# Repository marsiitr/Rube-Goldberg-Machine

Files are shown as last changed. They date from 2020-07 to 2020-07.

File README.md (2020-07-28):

<p align="justify">
  <h1>Rube-Goldberg-Machine</h1>
  <h2>Srishti 2020</h2>
</p>

<p align="center">
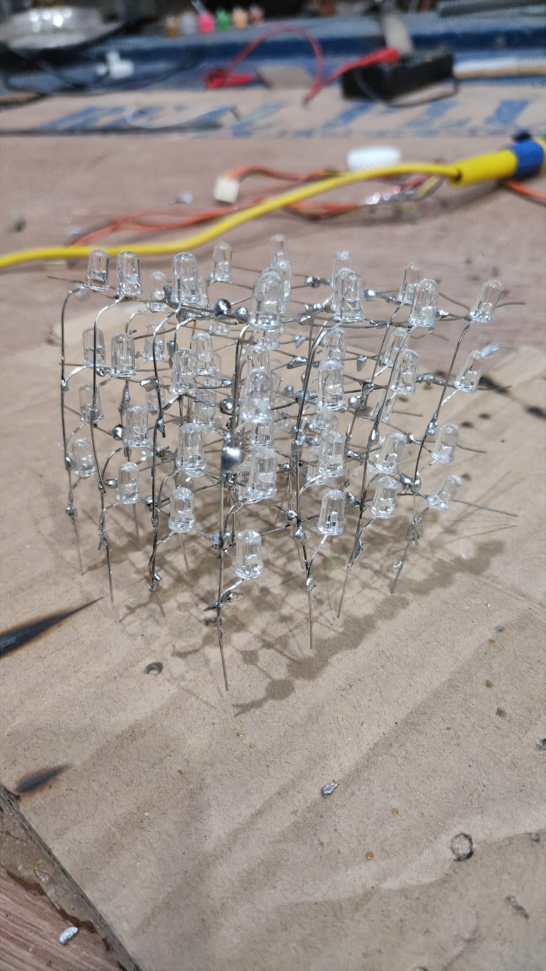
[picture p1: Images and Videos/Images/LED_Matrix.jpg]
LED Matrix
  
  <i>LED Matrix</i>
</p>

<p align="justify">
  <h2>Abstract</h2>
  <p>A Rube Goldberg Machine is a contraption intentionally designed to perform a simple task in an indirect and overly complicated way. The aim of this project is to depict the life of a college student through a similar complex assembly of mechanical and electronic components linked with each other creating a metaphor between humans and machines.</p>
</p>

<p align="justify">
  <h2>Motivation</h2>
  <p>College life may seem to be full of excitement and surprises for a layman, but little do he know of the struggles that the student had to face to reach that milestone and the difficulties that are masked by the brand college name. So our team of 5 freshers decided to cover the important moments of the journey beginning with exams to the major events of 1st year and what we think is to come next for us. We attempt to display it in a visually appealing format making use of our mechanical and electronics expertise.</p>
</p>

<p align="justify">
  <h2>Workflow</h2>
</p>

<p align="center">
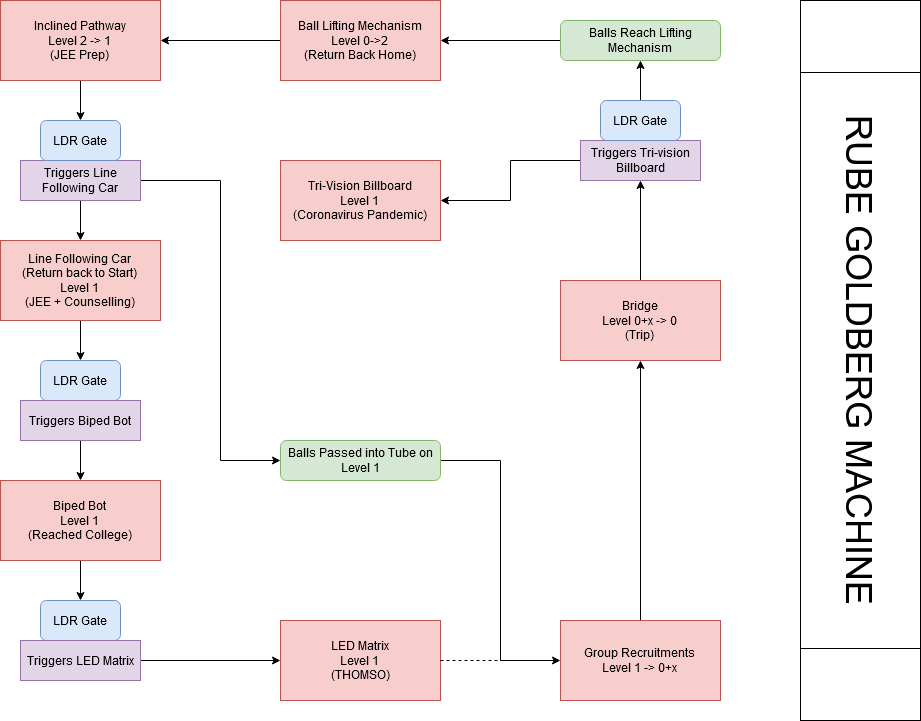
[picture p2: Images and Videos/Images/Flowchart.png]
Flowchart
  
  <i>Schematic Flow Chart of the Machine</i>
</p>

<p align="justify"> 
  
* The entire project is divided into 8 major elements depicting a distinct phase in the life of a student who is represented by spherical balls of different sizes. 

* The Tower of Exams(Inclined Pathway) illustrates the ups and downs, successes, and failures in each of the competitive exams. 

* The First LDR Gate represents the path to the major JEE Exam after which students seek admission to colleges through counselling and finally enter college after years of hard work.

* Similar to the biped bot, the students stumble here and there in the college exploring various things and then comes the first major college cultural fest of their lives, THOMSO, depicted using LED Cube. 

* Entering the next semester, students are overwhelmed with all the campus groups releasing recruitment notices.

* After this stressful and dilemmatic process comes the adventurous trip which is depicted by the bridge (Lakshman Jhula,  Rishikesh). 

* Next comes the second semester’s Mid-Term Examinations and following End-Term Examinations which is well shown by the Trivision Billboard. 

* Summer breaks are depicted by the Ball lifting mechanism and the journey goes on for the next and their next batch of freshers as our Rube Goldberg machine works in a loop.

</p>

<p align="justify">
  <h2>Mechanical Aspect of the Design</h2>
  <p>Rubber balls 3 of radius 2.5 cm and 3 of radius 3 cm each are used to denote the students.<br>The following steps help one understand the journey by providing a mechanical description of every component:
  <br>
  
* **Tower of Exams:** A vertical assembly of MDF towers inter-connected via loophole paths describes the difficult journey before getting into IIT.

  <p align="center">
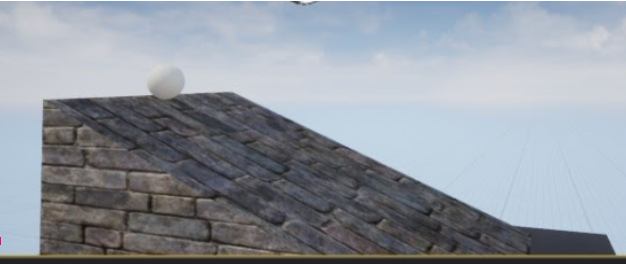
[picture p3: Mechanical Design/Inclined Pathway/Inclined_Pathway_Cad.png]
Tower of Exams
   <br>
    <i>Tower of Exams</i>
  </p>
  
* A smooth MDF path transitions into the LDR Gate triggering the **Line-following car**. Running on a parallel track is another MDF platform taking each ball to the chain lift.
  </p>

  <p align="center">
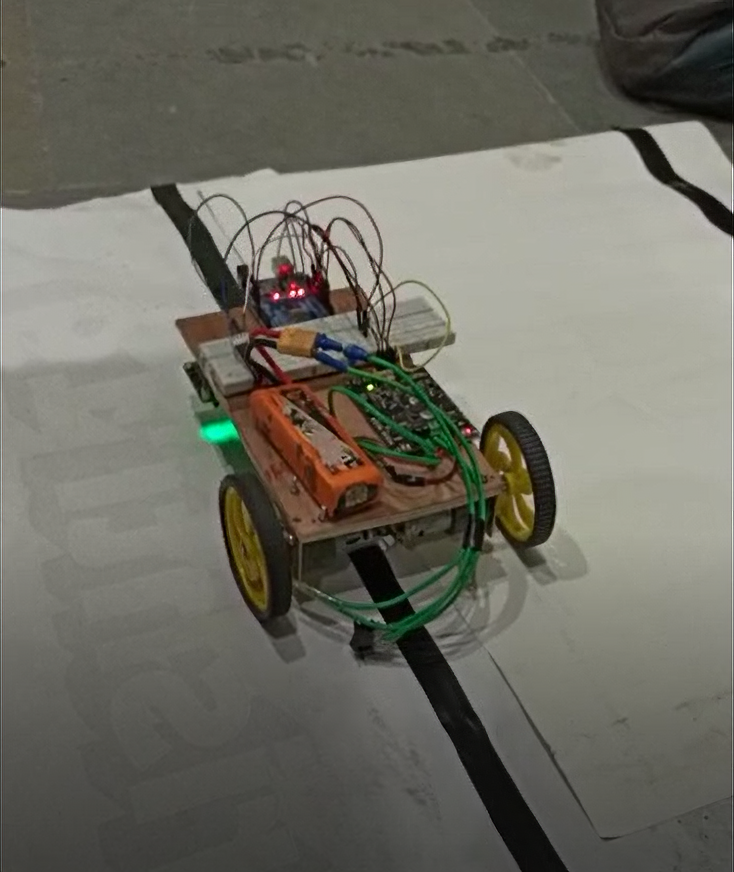
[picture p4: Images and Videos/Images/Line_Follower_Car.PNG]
Line Following Car
    <br>
    <i>Line Following Car</i>
  </p>

  <p>
 * Line-follower traverses through the loop and then triggers the Biped Bot.
  
 * **Biped bot** is a working prototype of a two-legged robot built with an assembly of 3 acrylic pulleys linked with elastic bands and 6mm steel rods, propelled by using a simple DC motor. It mounts an Arduino Uno on one side used to control the motor via a motor driver.
 
  </p>

<p align="center">
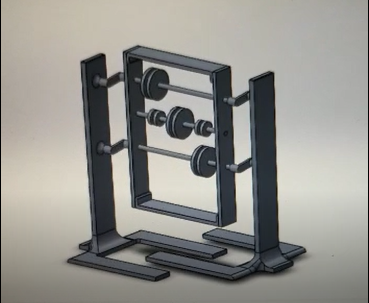
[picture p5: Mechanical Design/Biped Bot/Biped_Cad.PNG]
Biped Bot
  <br>
  <i>Biped Bot</i>
</p>

<p>
  
* Biped Bot passes through the LDR gate triggers the LED Matrix.

* Meanwhile, the balls approach the **Group Recruitment Phase** where they pass through a series of loopholes and get segregated as per their size.

<p align="center">
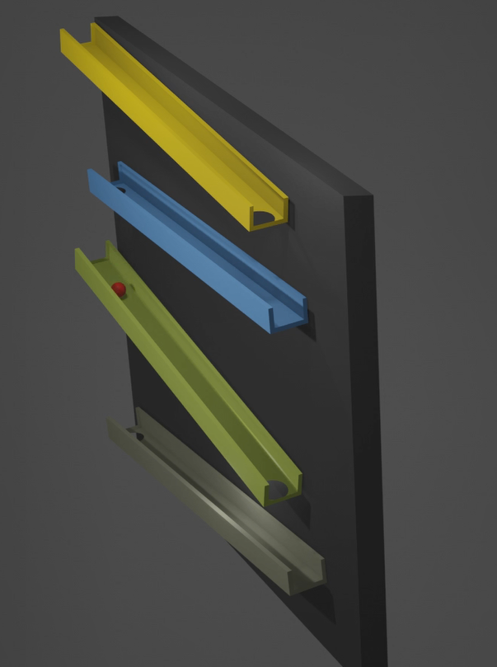
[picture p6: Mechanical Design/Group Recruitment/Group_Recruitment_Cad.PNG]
Group Recruitment Phase
  <br>
  <i>Group Recruitment Phase</i>
</p>

* The balls then trigger the final LDR gate activating the **Tri-Vision Billboard**.It is an assembly of 3 triangular prism-shaped boxes made using MDF and L-brackets mounted on a gear each through steel shafts held in place using a Plywood base and are free to rotate about its axis. A stepper motor is coupled with a driving gear, which transmits the actuation to all the three parts of the billboard, also employing two idler gears, so that all the prisms rotate in the same direction and in phase with each other. The gears and the base have been carefully 3d printed in the Tinkering Lab. [Reference](https://www.youtube.com/watch?v=uCx9riKxTvY&feature=youtu.be) (Heavily modified from the mentioned reference).

</p>

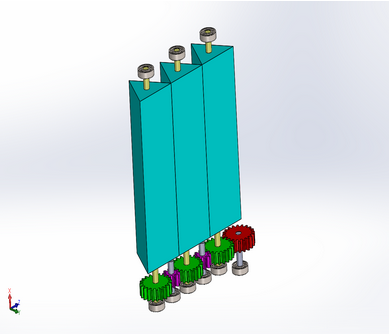
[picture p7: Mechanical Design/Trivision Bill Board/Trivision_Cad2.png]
Trivision Bill Board
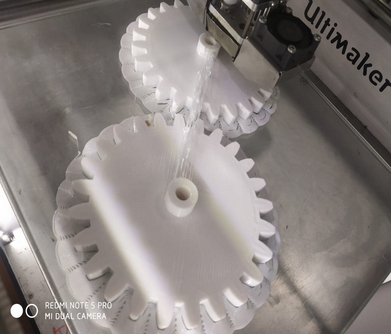
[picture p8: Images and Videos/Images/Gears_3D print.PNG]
Gear 3D print
 

<p>
  
* In the end, a **chain lift mechanism** lifts the balls back to level 1. The mechanism uses a 48-inch ladder chain and sprockets powered by a 12V DC motor. [Reference](https://www.youtube.com/watch?v=E2Yy66IbVuw&feature=youtu.be)
</p>
</p>

<p align="justify">
  <h2>Electronics Aspect of the Design</h2>
  <h3>Microcontroller</h3>
  <p>Arduino Uno 2560 R3 is used as the microcontroller board in each of the bots.</p>
  <h3>Hardware Architecture of the Line Following Car</h3>
</p>

<p align="center">
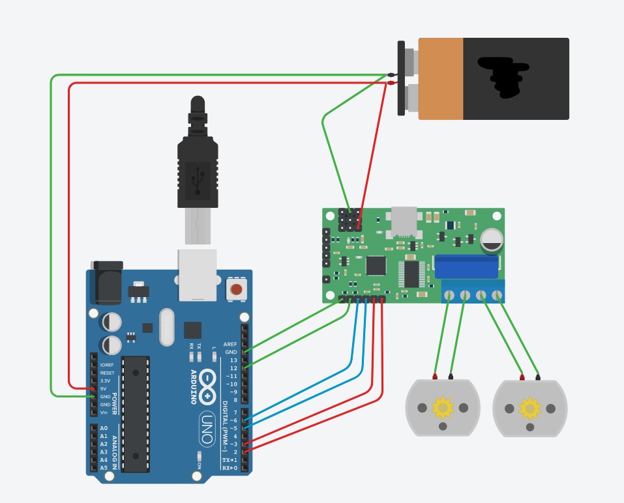
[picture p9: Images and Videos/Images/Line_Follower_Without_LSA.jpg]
Connections without the LSA
  <br>
  <i>Connections without the LSA</i>
</p>

### LSA Connections to Arduino
| LSA08 pin | Arduino Uno board |
|:-----:|:---:|
| 1 | RX (pin 0) |
| 2 | TX (pin 1)|
| 3 | Digital (pin 2) |
| 4 | Not Used |
| 5 | Digital (pin 4)|
| 6 | Not Used |
| 7 | Not Used|
| 8 | Not Used |
| 9 | Vin |
| 10 | GND |

<p align="justify">
  <h3>LSA08 Settings:</h3>
  <p>LINEMODE: Dark-ON detecting black line in white background.
  
  THRESHOLD: 7
  
  JUNCTION WIDTH: 8
  
  LSA gives 1 byte output data ranging from 0-70 with 35 being the base level.
  
  <h3>Working Principle</h3>
</p>

<p align="center">
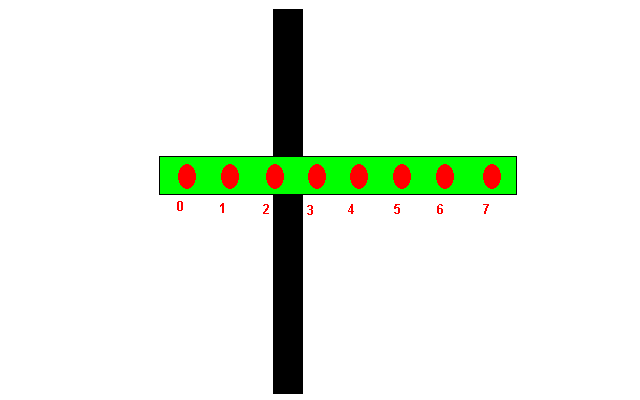
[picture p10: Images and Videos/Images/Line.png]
LSA Sensor Logic
  <br>
  <i>LSA Sensor Logic</i>
</p>

<p align="justify">
  <p>The car remains stable and follows the straight line if Level=35.
  For Level<35 : Speed of the left motor increases such that it comes back on track by moving to the right.
  For Level>35 : Speed of the right motor increases such that it comes back on track by moving to the left.</p>
    <h3>PID</h3>
    <p>PID is short for proportional, integral, and derivative. The PID is used to correct the error of the bot while traversing.
The correction value is given as
Correction = kp(error) + kd(error- previous_error)
<h3>Biped Bot</h3>
<p>A DC motor interconnected to three pulleys using bands which is responsible for the movement of a bipedal bot was driven by a motor driver which is connected to the Arduino Uno, battery, and also to HC-05 (which is used to pair Bluetooth) through a common ground. HC - 05 is also connected to the Arduino Uno through which the instructions given from the phone via Bluetooth can be transmitted to the Arduino Uno and so to the Motor Driver. The speed of the motor and direction can be controlled using the Bluetooth module.</p>

<p align="center">
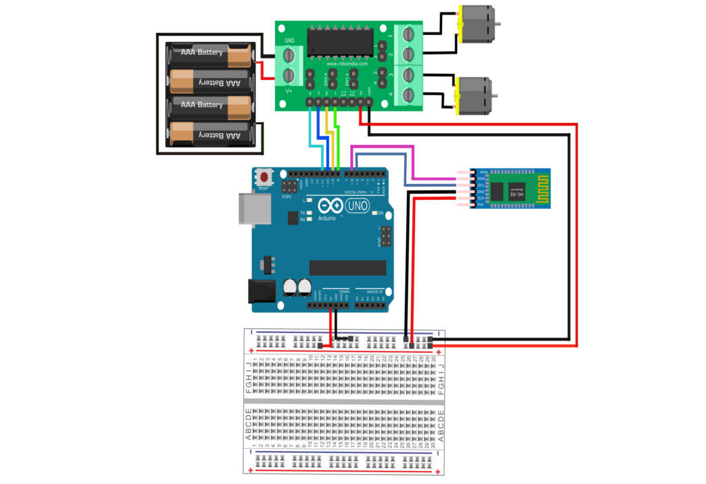
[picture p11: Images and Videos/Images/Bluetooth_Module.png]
Biped Bluetooth Module Connections
  <br>
  <i>Biped Bluetooth Module Connections</i>
</p>

<h3>LED Matrix</h3>
<p>It is a cube matrix built using 64 Light Emitting Diodes(LEDs, blue coloured) carefully soldered, and is capable of displaying various patterns as per the code fed into it.</p>

<h3>Trivision Billboard</h3>
<p>Uses a stepper motor to control the movement of the steel shafts about its axis controlled through the L298A motor driver.</p>

<h3>Chain Lift</h3>
<p>Uses a 12V DC Gear motor to rotate the chain vertically stabilized via sprockets.</p>

<p align="center">
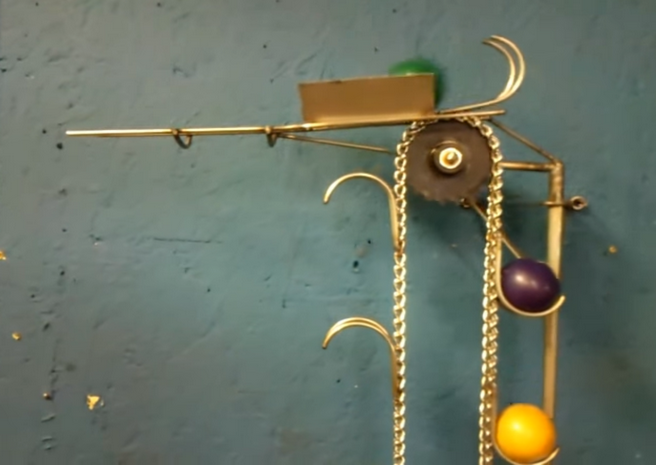
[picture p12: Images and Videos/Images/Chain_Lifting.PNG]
Chain Lift
  <br>
  <i>Chain Lift</i>
</p>

<h3>LDR Gate</h3>
<p>A simple setup of an LDR along with an Arduino Uno board is used to trigger elements in various places throughout the loop.</p>
<p align="center">
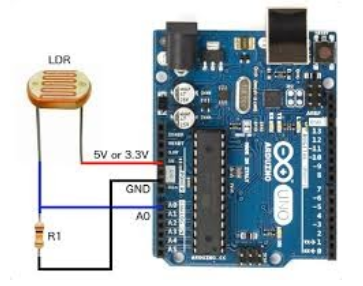
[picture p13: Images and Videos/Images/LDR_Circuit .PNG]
LDR
  <br>
  <i>LDR Connections</i>
</p>

<h3>Motor Driver</h3>
<p>We have used the Cytron MDD10A and L298A motor drivers. MDD10A is a dual-channel version of the MDD10C. Like MDD10C, MDD10A also supports locked-antiphase and sign-magnitude PWM signal.</p>
</p>

<p align="justify">
  <h2>Cost Structure</h2>
</p>

| Components | Quantity | Cost (in INR) |
|:---:|:---:|:---:|
| Auto-Calibrating Line Sensor LSA08 | 1 | 5000 |
| Arduino Uno Rev3 | 5 | 2000 |
| Digital LDR Module | 4 | 400 |
| LED | 64 | 100 |
| Cytron Dual Channel Enhanced 13Amp DC Motor Driver | 4 | 8000 |
| LiPo Battery 11.1V | 5 | 1500 |
| Motor Bracket | 2 | 200 |
| DC Motor | 1 | 300 |
| Stepper Motor | 1 | 500 |
| HC-05 | 1 | 300 |
| 48 inch Stainless Steel Ladder Chain | 1 | 1000 |
|Other components| | 1000  |
|Total Cost| | 20300  |

<p align="justify">
  
  <h2>Applications</h2>
  <p>The project succeeds in providing a visual description of a student's life.</p>
  
  <h2>Limitations</h2>
  
  <p>
  
* Some of the systems are not mechanically and electronically robust. For eg: The platforms used to carry the balls are hand-crafted and hence prone to obstruct the paths.

* Although an attempt was made to automate all the things and create a loop, several phases in the project still require manual handling. For eg: We need to collect the balls sorted and collected in the group recruitment phase and place them back in the starting point.

* Due to the Covid-19 pandemic, the actual Srishti event got cancelled. This created the most terrible impact as our team could not manufacture some of the parts like the chain lift mechanism. 
</p>
<h2>Future Improvement</h2>
<p>
  
* Manufacture the remaining components and make the project display-ready.

* Include several components for automating the process. A Ball-collecting bot making use of OpenCV for ball detection can be made to address this issue. It will significantly help to reduce the amount of manual work required to make the platforms.

</p>
<h2>Team Members</h2>

<p>
  
1. [Pradnesh Chavan](https://github.com/prady39)
2. [Rohit Kulkarni](https://github.com/roku01)               
3. [Shruti Gour](https://github.com/ShrutiGour)
4. [Shubham Kumar](https://github.com/shubhamr2701)
5. [Stuti Lilani](https://github.com/stuts23)
  
</p>
<h2>Mentors</h2>
<p>
  
1. [Kshitij Bithel](https://github.com/KSHITIJBITHEL)
2. Tabish Madni
3. [Yashutosh Bansal](https://github.com/yashutoshbansal)

</p>
<h2>References</h2>

<p>
  
- [Chain Lift](https://www.youtube.com/watch?v=E2Yy66IbVuw&feature=youtu.be)
- [Tri Vision Bill Board](https://www.youtube.com/watch?v=uCx9riKxTvY&feature=youtu.be)
- [Bluetooth Module](https://roboindia.com/tutorials/motor-control-with-bluetooth-module-hc-05/)
- [Line Follower Simulation](https://www.youtube.com/watch?v=vfwxKjOr-7o)
- [Line Following Car](https://tutorial.cytron.io/2015/07/31/line-following-robot-using-lsa08-serial-mode-digital-output/)

</p>

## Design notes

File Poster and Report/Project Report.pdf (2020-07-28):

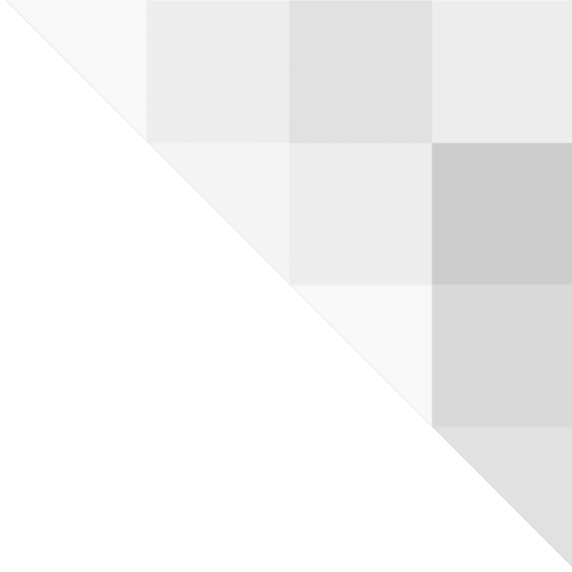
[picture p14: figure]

# Rube Goldberg Machine

# Srishti 2020

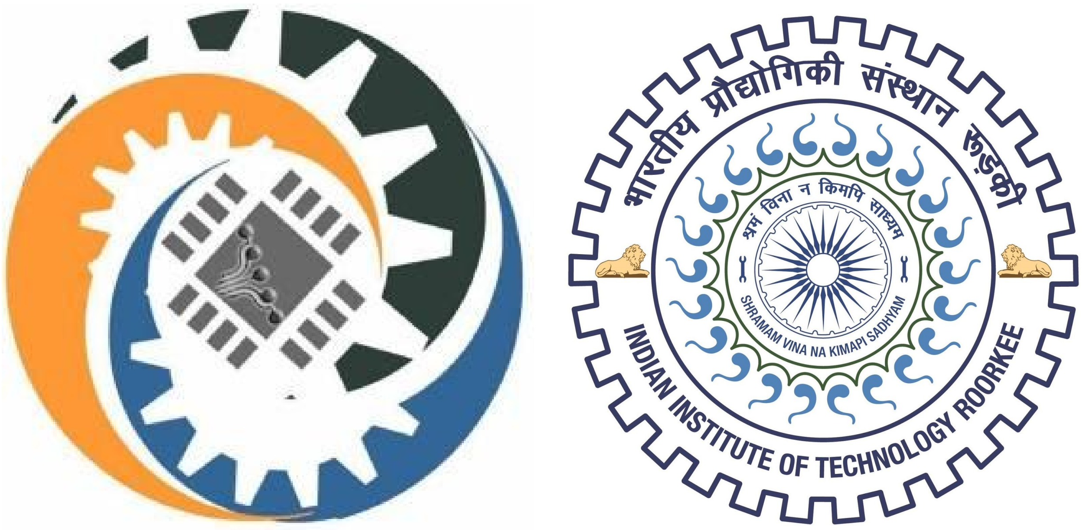
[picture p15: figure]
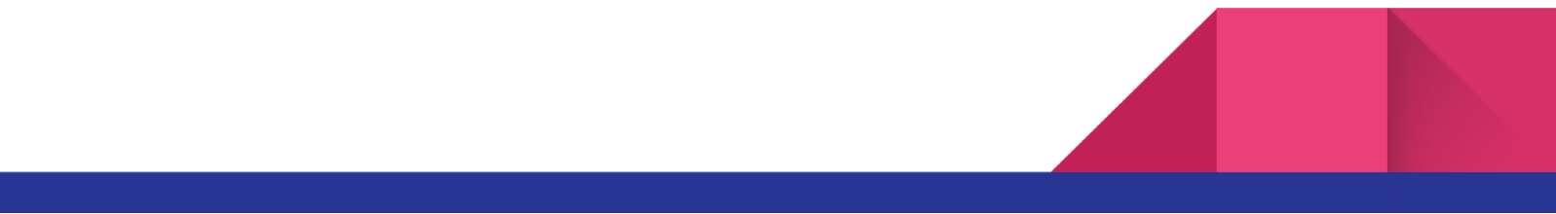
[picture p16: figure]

# Team Members

## Pradnesh Chavan Rohit Kulkarni Shruti Gour Shubham Raut Stuti Lilani

# Mentors

## Kshitij Bithel Tabish Madni Yashutosh Bansal

# Contents

## ➔Abstract ➔Project Motivation ➔Elements and Linkages ➔Mechanical Aspects of the Project ➔Electronics Aspects of the Project ➔Cost Structure ➔Applications ➔Limitations ➔Future Improvement ➔Acknowledgments

# Abstract

A Rube Goldberg Machine is a contraption intentionally designed to perform a simple task in an indirect and overly complicated way. The aim of this project is to depict the life of a college student through a similar complex assembly of mechanical and electronic components linked with each other creating a metaphor between humans and machines.

# Project Motivation

College life may seem to be full of excitement and surprises for many, but little do they know of the struggles that the student had to face to reach that milestone and the difficulties that are masked by the brand college name. So our team of 5 freshers decided to cover the important moments of the journey beginning with exams to the major events of 1st year and what we think is to come next for us. We attempt to display it in a visually appealing format making use of our mechanical and electronics expertise.

# Elements and Linkages

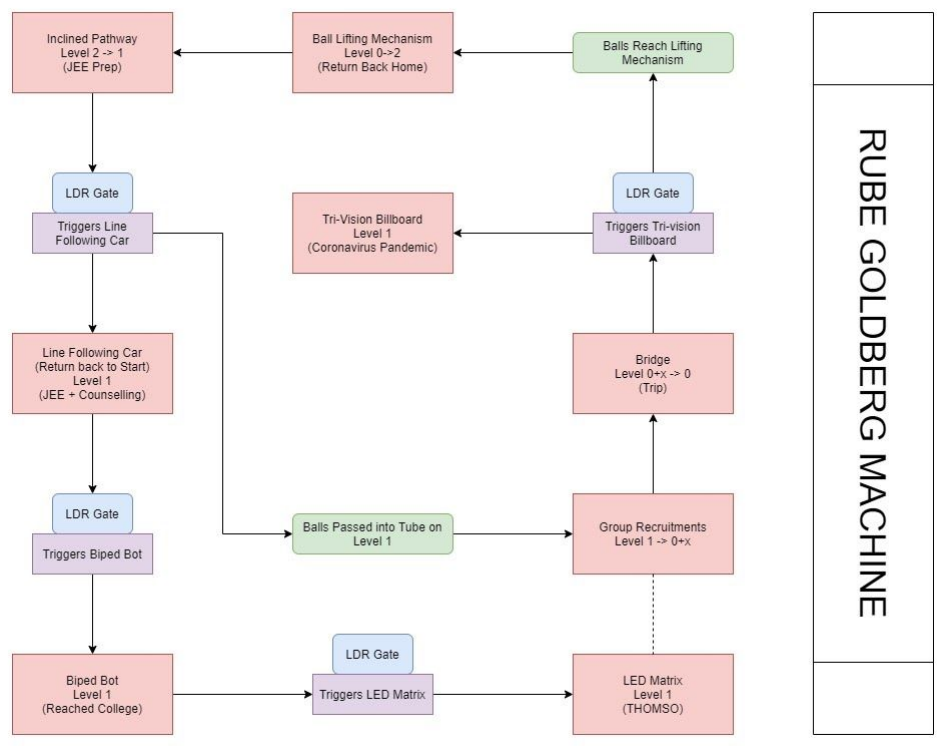
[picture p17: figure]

- The entire project is divided into 8 major elements depicting a distinct phase in the life of a student who is represented by spherical balls of different sizes.
- The Tower of Exams(Inclined Pathway) illustrates the ups and downs, successes, and failures in each of the competitive exams.
- The First LDR Gate represents the path to the major JEE Exam after which students seek admission to colleges through counseling and finally enter college after years of hard work.
- Similar to the biped bot, the students stumble here and there in the college exploring various things many of which are new to them and then comes the first major college fest of their lives, THOMSO, depicted using LED Cube. The matrix laden with its bright colors succeeds in depicting the aura of the fest.
- Entering the next semester, students are overwhelmed with all the groups releasing recruitment notices. This period involves a lot of stress and confusion, but it is fun nevertheless.
- After this stressful and dilemmatic process comes the adventurous trip which is depicted by the bridge (Lakshman Jhula, Rishikesh).
- Next comes the second semester’s Mid-Term Examinations and following End-Term Examinations which is well shown by the Trivision Billboard.
- Then we all head back to our respective hometowns for spending the summer breaks that are depicted by the Ball lifting mechanism and the journey goes on for the next and their next batch of freshers as our Rube Goldberg machine works in a loop.

# Mechanical Aspect of the Design

Rubber balls 3 of radius 2.5cm and 3 of radius 3cm each are used to denote the students.
The following steps help one understand the journey by providing a mechanical description of every component:
1. Tower of Exams: A vertical assembly of MDF towers inter-connected via loophole paths describes the difficult journey before getting into IIT.

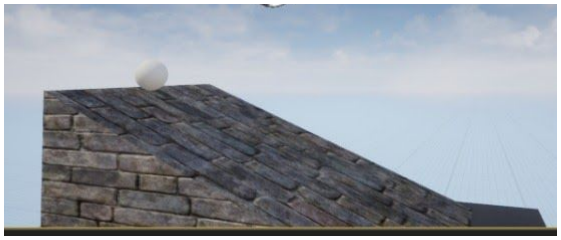
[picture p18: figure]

2. A smooth MDF path transitions into the LDR Gate triggering the Line-Following Car. Running on a parallel track is another MDF platform taking each ball to the chain lift. Line-follower traverses through the LDR gate and then triggers the Biped Bot.

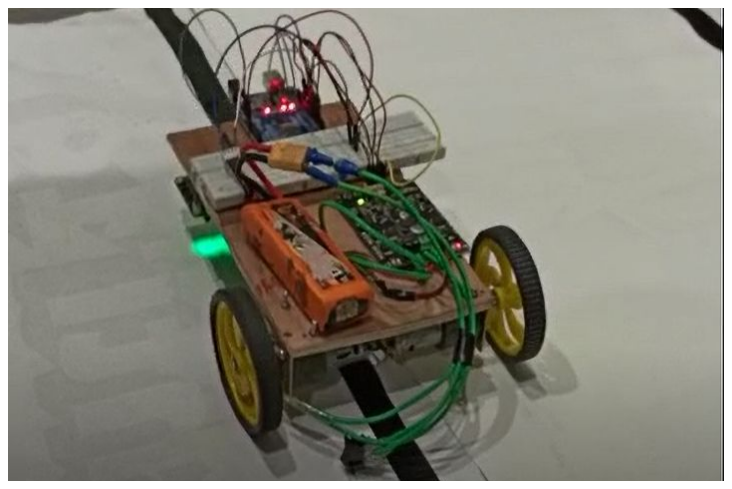
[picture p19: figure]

3. Biped bot is a working prototype of a two-legged robot contained in an MDF frame with an assembly of 3 big and 2 small acrylic pulleys linked with elastic bands and held in place by 6mm shafts, propelled by using a simple DC motor. It mounts an Arduino Uno on one side to control the motor via a motor driver. Reference (https://youtu.be/Z7N0xCDVzIA)

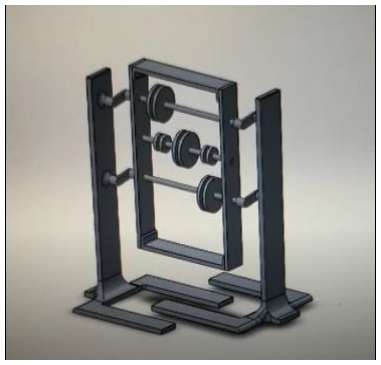
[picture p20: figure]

4. The Biped Bot passes through the LDR gate and triggers the | LED Matrix | .

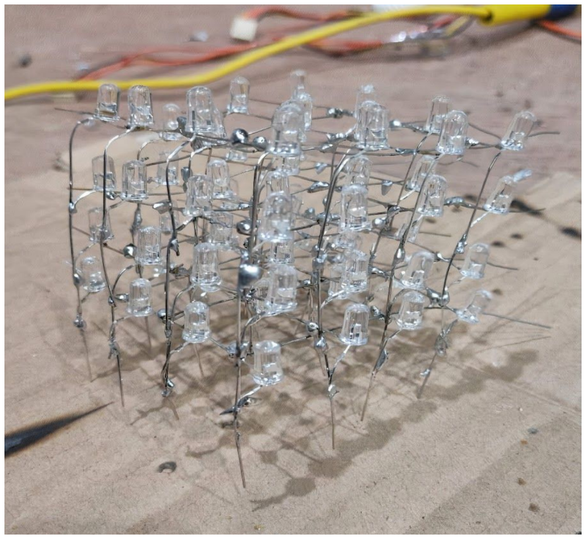
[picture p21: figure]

5. Meanwhile, the balls approach the Group Recruitment Phase where they pass through a series of inclined ramps that contain holes at their ends and get segregated along the way as per their size. This symbolizes the segregation of students into various tech and cultural groups based on their skills and interests.

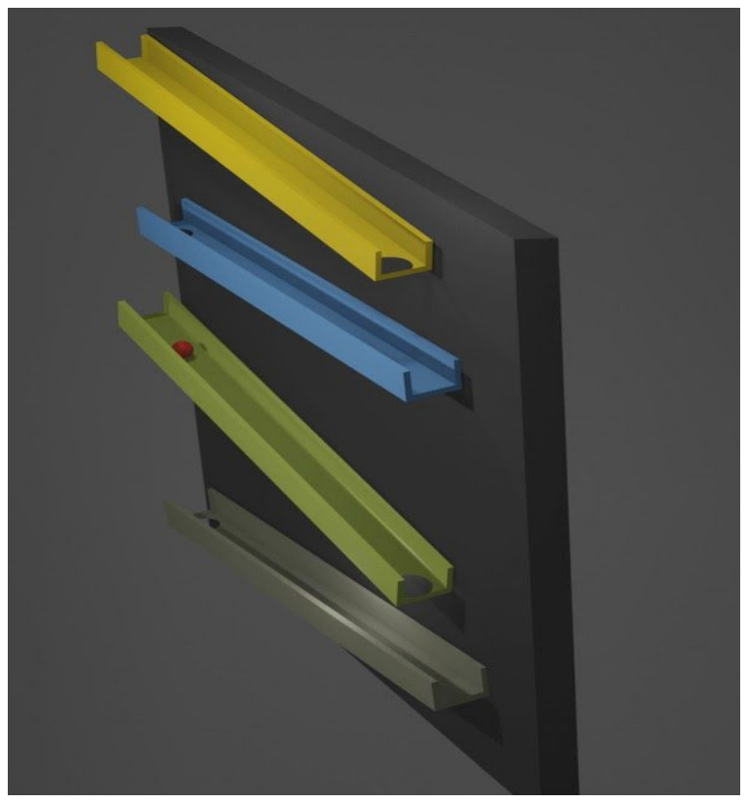
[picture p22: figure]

6. The balls emerge from the Group Recruitments at a certain height above the ground level and roll down a slope passing through a simple bridge made using cardboard. This signifies the trips that students go on after the onset of the spring season. After this, the balls pass through another LDR gate and trigger the next element.
7. Balls then trigger the final LDR gate activating the Tri-Vision Billboard . It is an assembly of 3 triangular prism-shaped boxes made using MDF and L-brackets mounted on a gear each through steel shafts held in place using a Plywood base and are free to rotate about its axis. A stepper motor is coupled with a driving gear, which transmits the actuation to all the three parts of the billboard, also employing two idler gears, so that all the prisms rotate in the same direction and in phase with each other. The gears and the base have been carefully 3d printed using PLA in the Tinkering Lab. Reference (https://youtu.be/uCx9riKxTvY) (Heavily modified from the aforementioned).

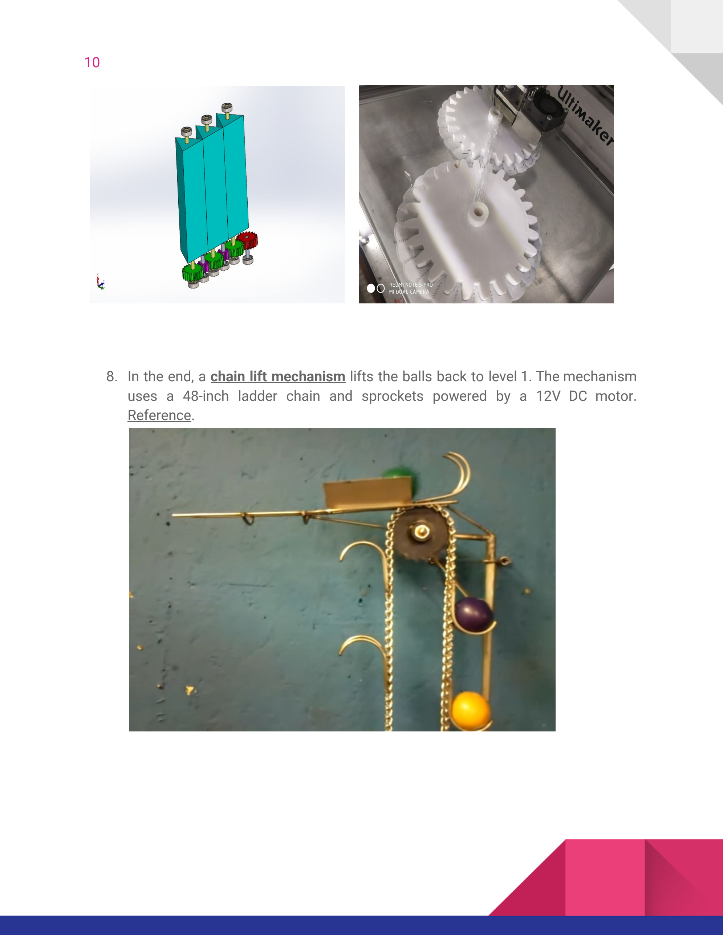
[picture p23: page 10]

8. In the end, a chain lift mechanism lifts the balls back to level 1. The mechanism uses a 48-inch ladder chain and sprockets powered by a 12V DC motor. Reference (https://www.youtube.com/watch?v=E2Yy66IbVuw&feature=youtu.be) .

# Electronics Aspect of the Design

Microcontroller: Arduino Uno 2560 R3 is used as the microcontroller board in each of the bots.

## Line Following Car:

Hardware Architecture of the Line Following Car:

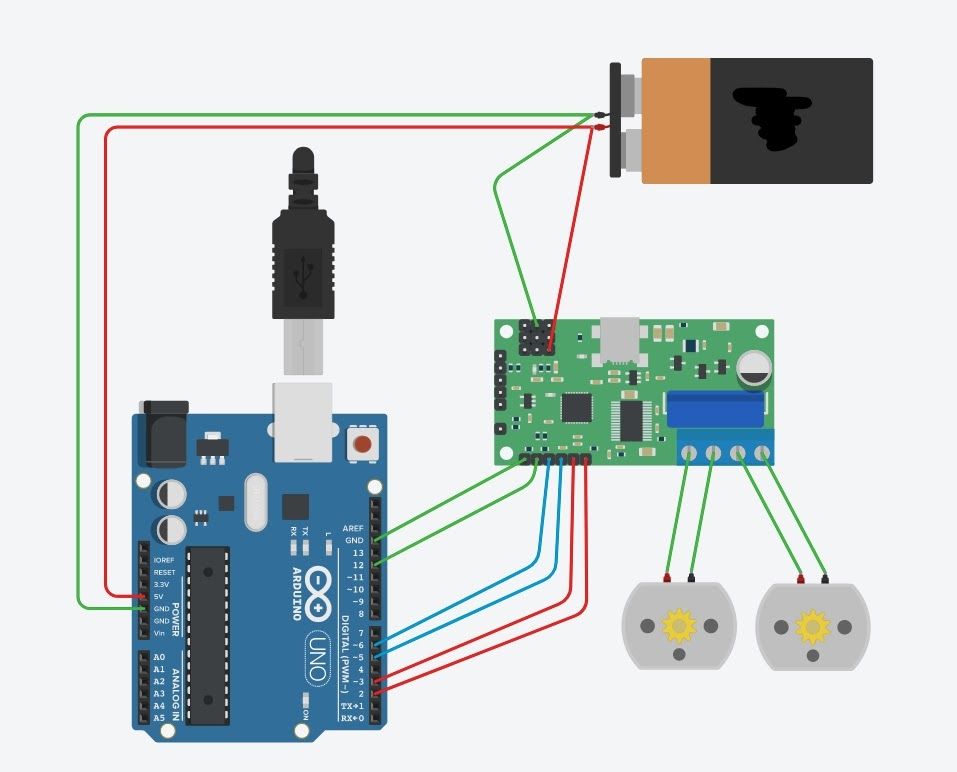
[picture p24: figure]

LSA CONNECTION TO ARDUINO

LSA08 Pin | Arduino Uno board
1 | RX (pin 0)
2 | TX (pin 1)
3 | Digital pin 2
4 | Not Used
5 | Digital pin 4
6 | Not Used
7 | Not Used
8 | Not Used
9 | Vin
10 | GND

LSA08 Settings:
LINEMODE: Dark-ON detecting black line in white background.
THRESHOLD: 7
JUNCTION WIDTH: 8

LSA gives 1-byte output data ranging from 0-70 with 35 being the base level.

Working Principle:

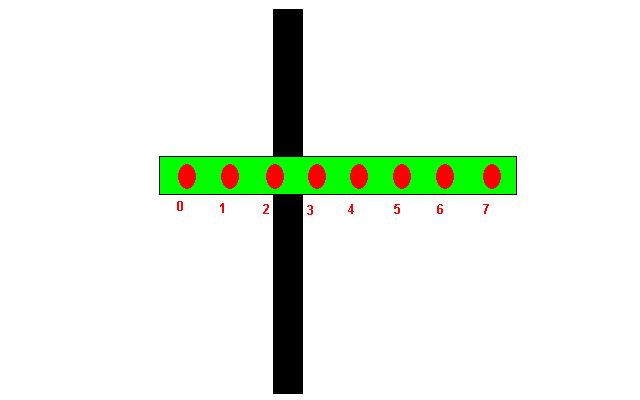
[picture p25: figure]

The car remains stable and follows the straight line if Level=35.
For Level<35: Speed of the left motor increases such that it comes back on track by moving to the right.
For Level>35: Speed of the right motor increases such that it comes back on track by moving to the left.

PID:

PID is short for proportional, integral, and derivative. The PID is used to correct the error of the bot while traversing.

The correction value is given as

Correction = kp(error) + kd(error- previous_error)

## Biped Bot:

A DC motor interconnected to three pulleys using bands which is responsible for the movement of a bipedal bot was driven by a motor driver which is connected to the Arduino Uno, battery, and also to HC-05 (which is used to pair Bluetooth) through a common ground. HC - 05 is also connected to the Arduino Uno through which the instructions given from the phone via Bluetooth can be transmitted to the Arduino Uno and so to the Motor Driver. The speed of the motor and direction can be controlled using the Bluetooth module.

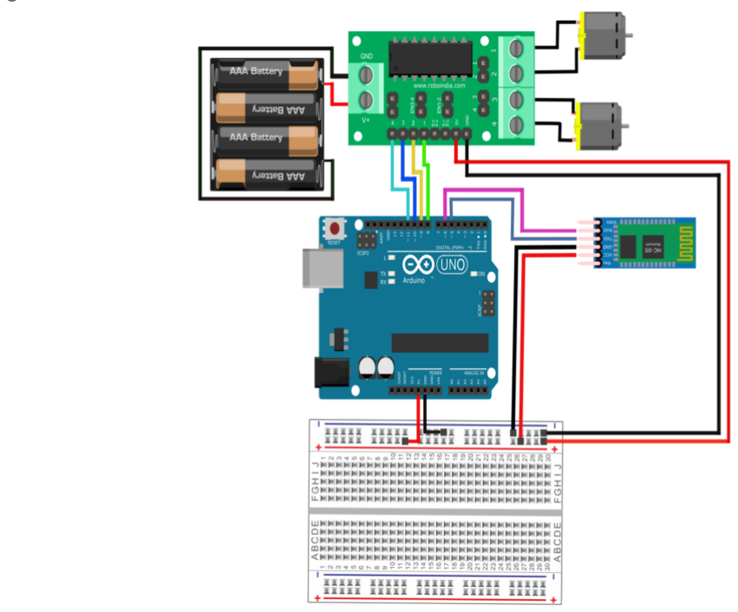
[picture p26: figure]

## LED Matrix:

It is a cube matrix built using 64 Light Emitting Diodes(LEDs, blue colored) carefully soldered, and is capable of displaying various patterns as per the code fed into it using the Arduino Mega board.
The positive terminals of all 4 LEDs in a vertical line are connected to each other and form a node. And the negative terminals of all the LEDs in a horizontal layer are connected. This results in 16 positive nodes and 4 negative nodes, connected to different pins on the Arduino Mega board. Each LED can be controlled individually or collectively along with other LEDs, depending upon the code. Reference (https://youtu.be/hjrfa04KPYI)

## Tri Vision BillBoard:

Uses a stepper motor to control the movement of the steel shafts about its axis controlled through the L298A motor driver, triggered by balls passing through the LDR gate.

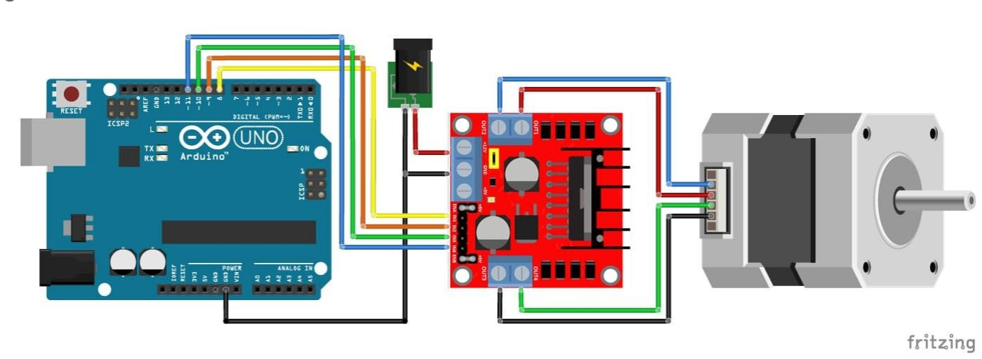
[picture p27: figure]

## Chain Lift:

Uses a 12V DC Gear motor to rotate the chain vertically stabilized via sprockets.

## LDR Gates:

A simple setup of an LDR along with an Arduino Uno board is used to trigger elements in various places throughout the loop. Reference (https://www.tweaking4all.com/hardware/arduino/arduino-light-sensitive-resistor/)

## Motor Driver:

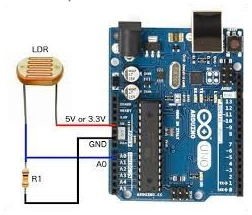
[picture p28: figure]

We have used the Cytron MDD10A and L298A motor drivers. MDD10A is a dual-channel version of the MDD10C. Like MD10C, MDD10A also supports a locked-antiphase and sign-magnitude PWM signal.

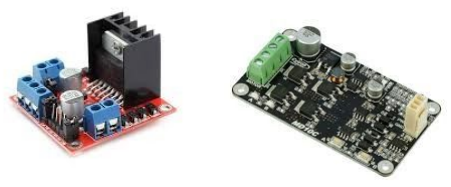
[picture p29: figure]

# Cost Structure

Components | Quantity | Cost (in INR)
Auto-Calibrating Line Sensor LSA08 | 1 | 5000
Arduino Uno Rev3 | 5 | 2000
Digital LDR Module | 4 | 400
LED | 64 | 100
Motor Driver | 4 | 8000
LiPo Battery 11.1V | 5 | 1500
Motor Bracket | 2 | 200
DC Motor | 1 | 300
Stepper Motor | 1 | 500
HC-05 | 1 | 300
48-inch Stainless Steel Ladder Chain | 1 | 1000
Other components | | 1000
TOTAL | | 20300

# Applications

The project succeeds in providing a visual description of a student’s life.

# Limitations

- Some of the systems are not mechanically and electronically robust. For eg: The platforms used to carry the balls are hand-crafted and hence prone to obstruct the paths.
- Although an attempt was made to automate all the things and create a loop, several phases in the project still require manual handling. For eg: We need to collect the balls sorted and collected in the group recruitment phase and place them back in the starting point.
- Due to the Covid-19 pandemic, the actual Srishti event got canceled. This created the most terrible impact as our team could not manufacture some of the parts like the chain lift mechanism.

# Future Improvement

- Manufacture the remaining components and make the project display-ready.
- Include several components for automating the process. A Ball-collecting robot making use of OpenCV for ball detection can be made to address this issue. It will significantly help to reduce the amount of manual work required to make the platforms.

# Acknowledgment

We would like to thank the Indian Institute of Technology Roorkee Administration and Student Technical Council for providing us an opportunity to do this project and show our skills by organizing Srishti, our Annual Technical Exhibition. We would also like to thank the Models and Robotics Section, IIT Roorkee for mentoring us and providing the components and tools for the project.

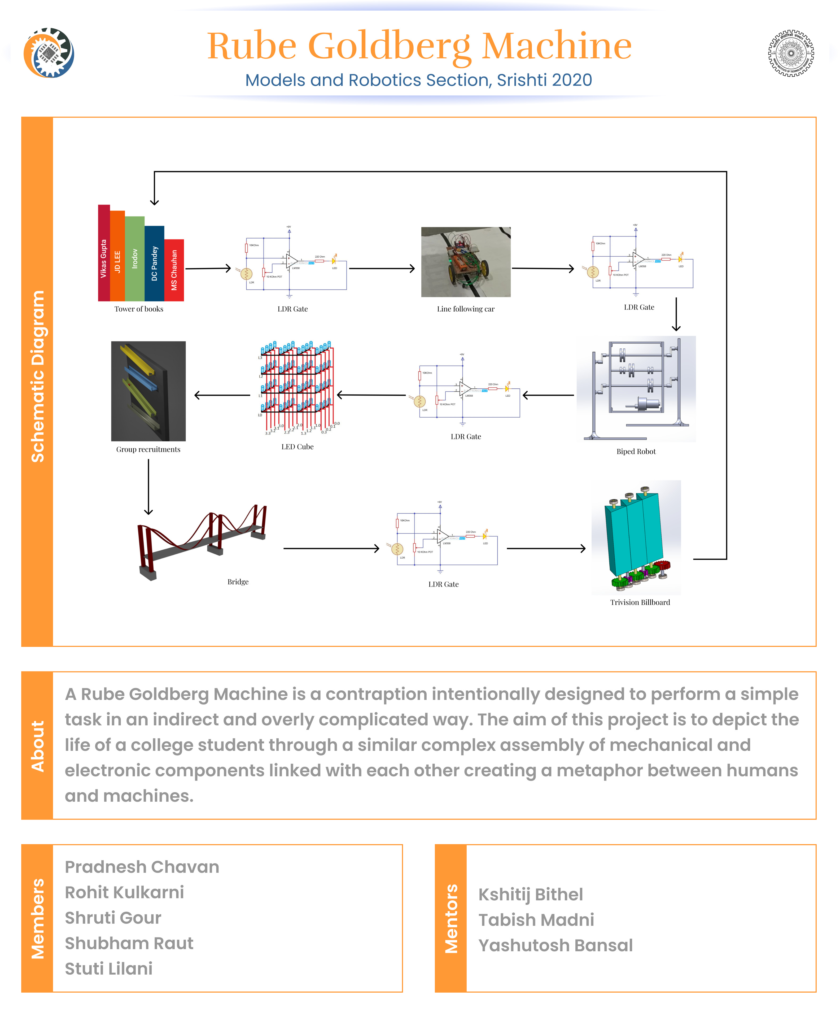
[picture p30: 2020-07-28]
Poster and Report/Poster.jpeg

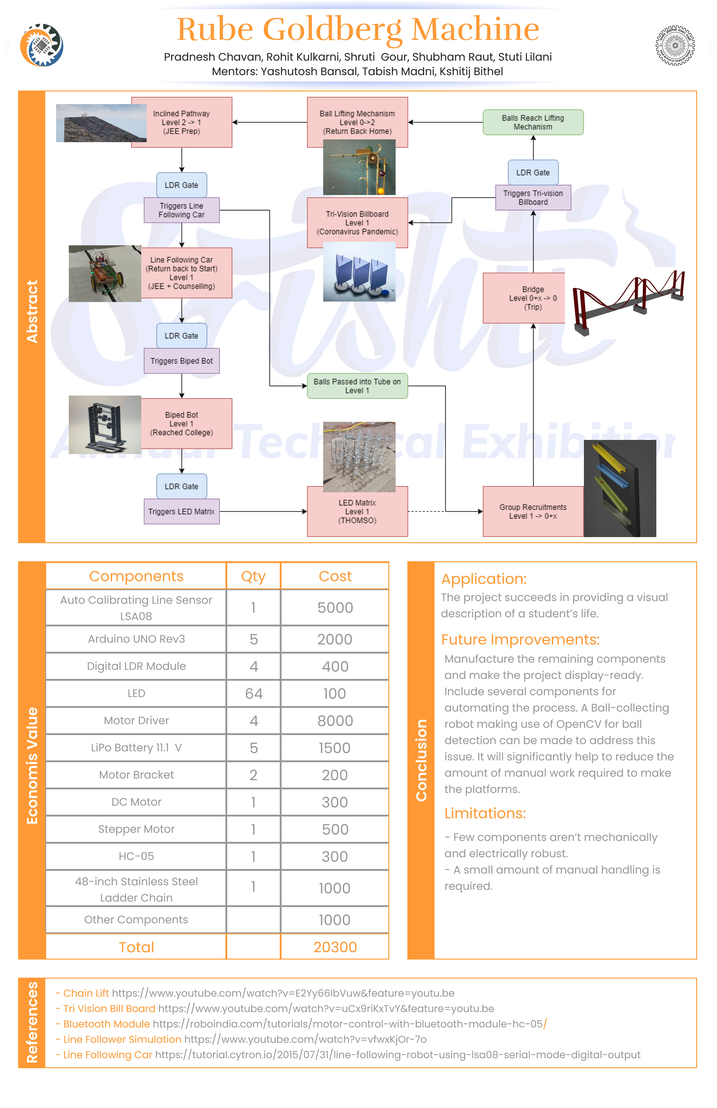
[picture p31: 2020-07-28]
Poster and Report/Presentation.jpeg

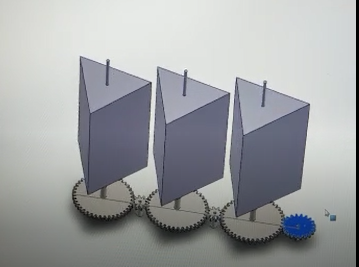
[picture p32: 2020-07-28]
Mechanical Design/Trivision Bill Board/Trivision_Cad.PNG

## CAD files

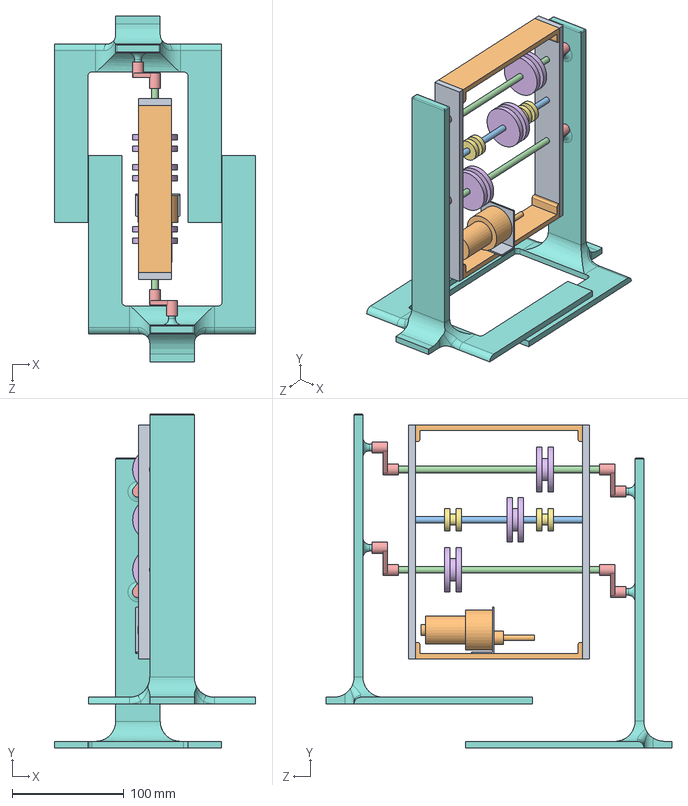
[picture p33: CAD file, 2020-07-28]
Mechanical Design/Biped Bot/Assembly.SLDASM
180.6 x 299.6 x 310.0 mm
Side Body x 2
Top & Base x 2
Central Shaft
Shaft x 2
Coupling x 4
Gear (1,2) x 3
Gear (0.5,1) x 2
Leg x 2
Motor Mount
Motor

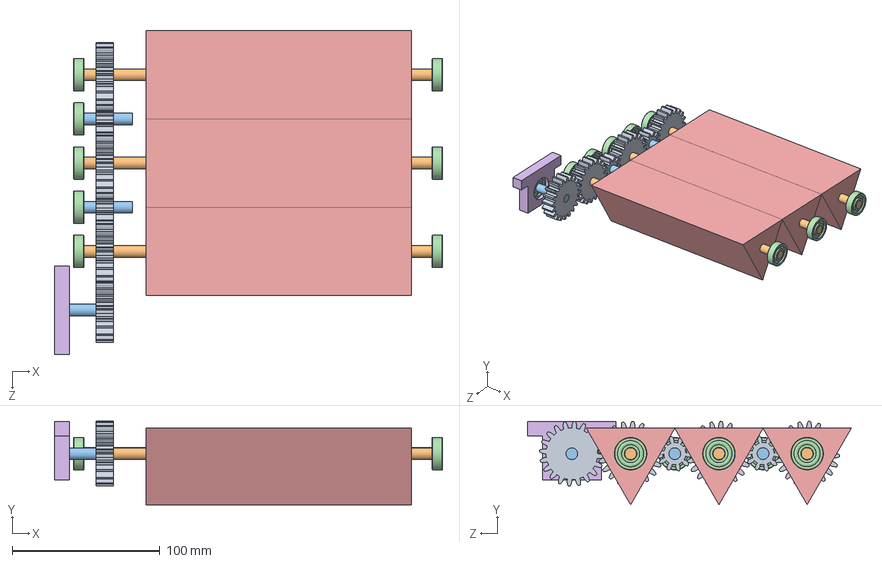
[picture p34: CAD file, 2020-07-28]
Mechanical Design/Trivision Bill Board/Assem1.SLDASM
262.9 x 56.7 x 219.4 mm
spur gear_am x 6
8mm shaft 25cm x 3
shaft 8mm 4cm x 3
radial ball bearing_68_am x 9
triangle 18cm x 3

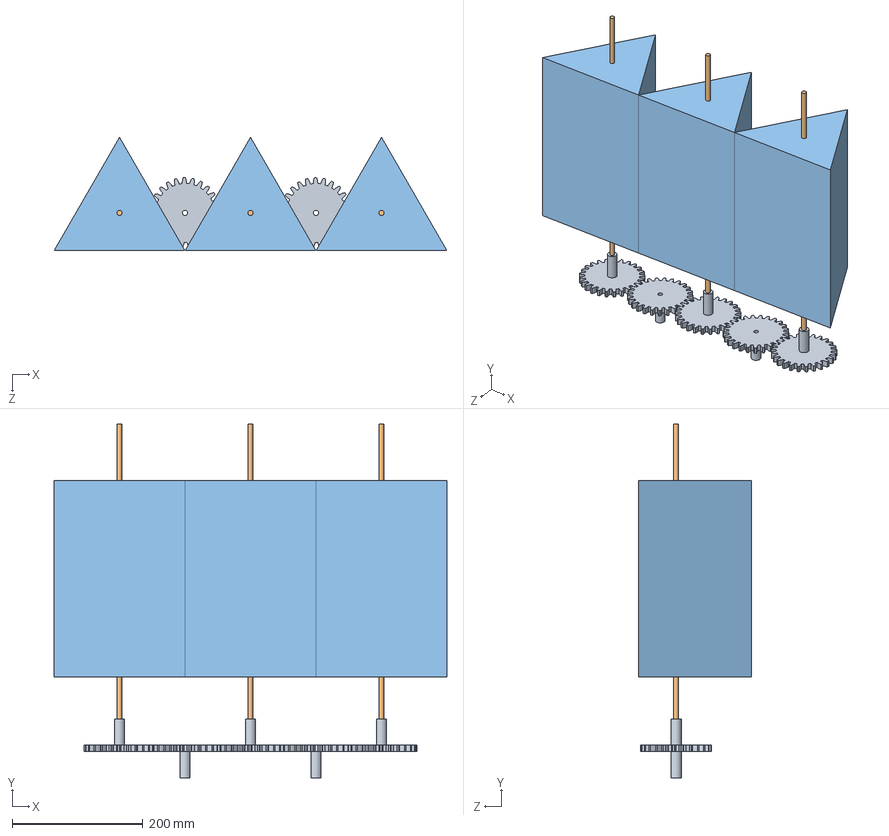
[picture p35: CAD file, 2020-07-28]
Mechanical Design/Trivision Bill Board/Assembly1.SLDASM
600.0 x 540.0 x 173.2 mm
spur gear_am x 5
shaft 500mmL 8mmD x 3
Triangular Prism x 3

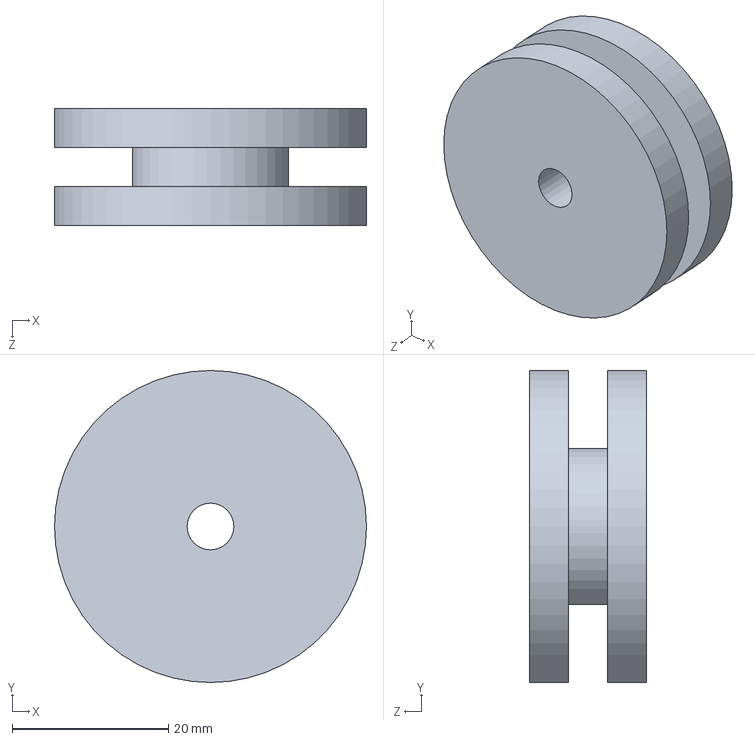
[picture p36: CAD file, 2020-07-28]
Mechanical Design/Biped Bot/Gear (1,2).SLDPRT
40.0 x 40.0 x 15.0 mm

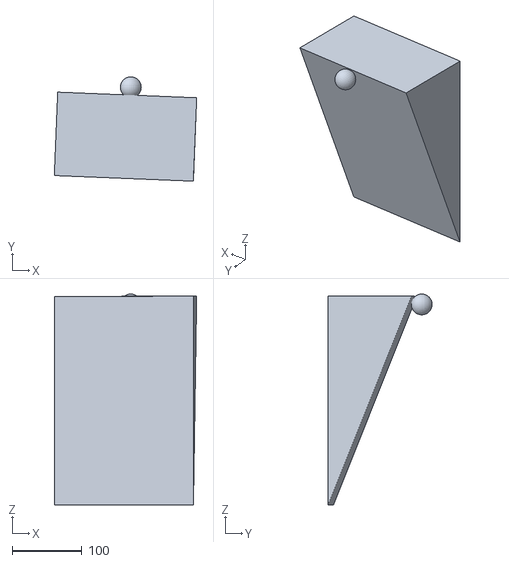
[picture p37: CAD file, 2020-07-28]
Mechanical Design/Inclined Pathway/Inclined_Pathway_Cad.OBJ
204.7 x 150.0 x 303.3

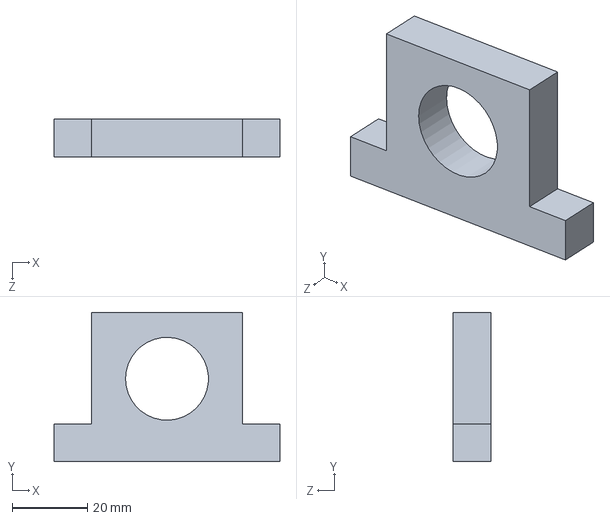
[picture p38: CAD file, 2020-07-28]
Mechanical Design/Trivision Bill Board/bearing block.SLDPRT
60.0 x 39.7 x 10.0 mm

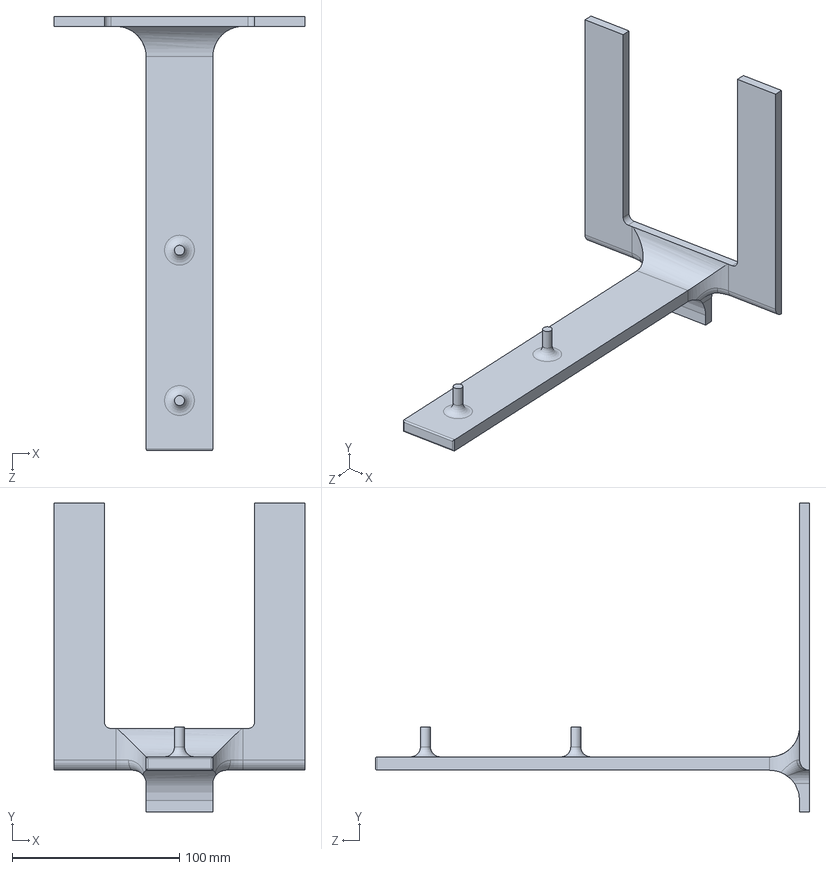
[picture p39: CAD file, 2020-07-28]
Mechanical Design/Biped Bot/Leg.SLDPRT
150.0 x 185.0 x 260.0 mm

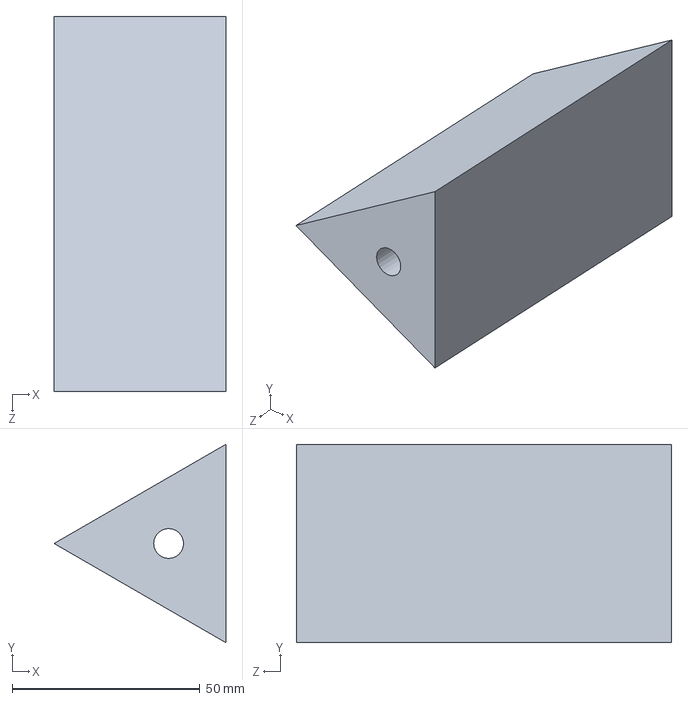
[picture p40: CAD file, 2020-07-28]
Mechanical Design/Trivision Bill Board/triangle.SLDPRT
45.8 x 52.9 x 100.0 mm

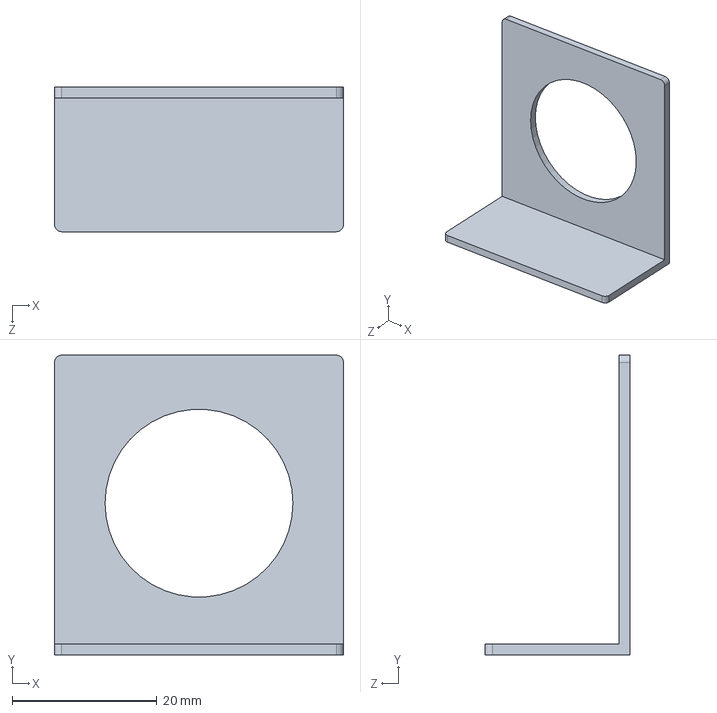
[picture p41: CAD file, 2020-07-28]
Mechanical Design/Biped Bot/Motor Mount.SLDPRT
40.0 x 41.5 x 20.0 mm

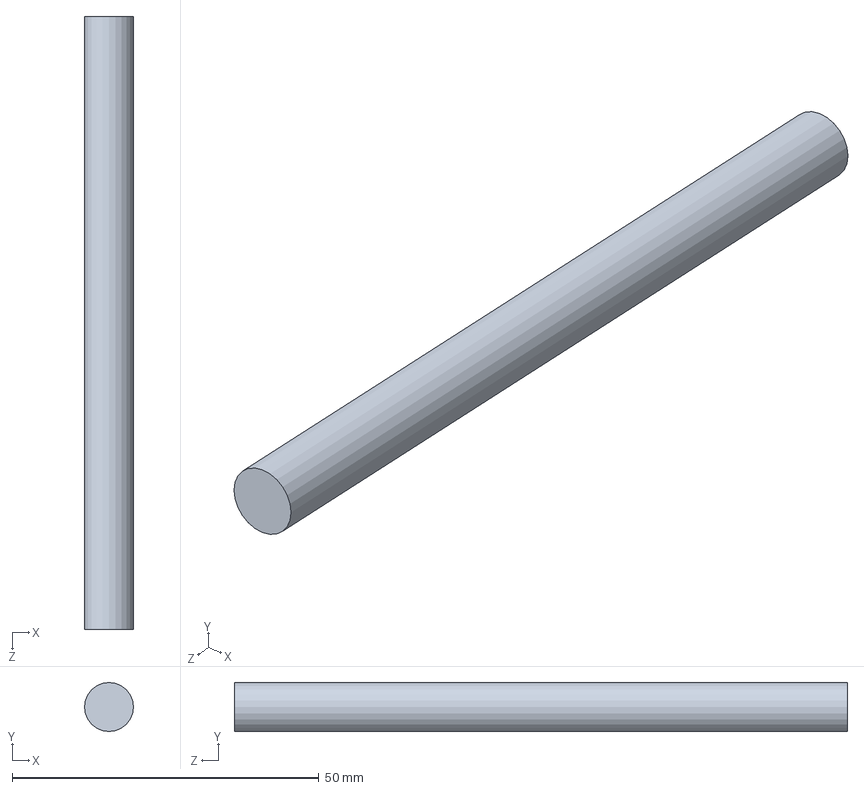
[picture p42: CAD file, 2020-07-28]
Mechanical Design/Trivision Bill Board/shaft 8mm 10 cm.SLDPRT
8.00 x 8.00 x 100.0 mm

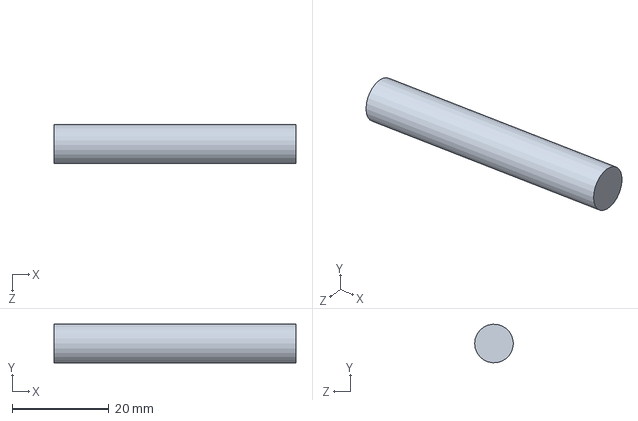
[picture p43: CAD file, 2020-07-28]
Mechanical Design/Trivision Bill Board/shaft 8mm.SLDPRT
50.0 x 7.98 x 8.00 mm

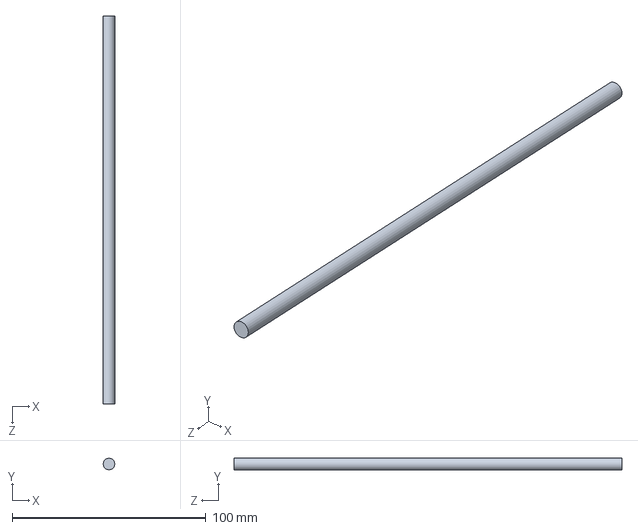
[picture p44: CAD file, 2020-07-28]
Mechanical Design/Biped Bot/Shaft.SLDPRT
6.00 x 6.00 x 200.0 mm

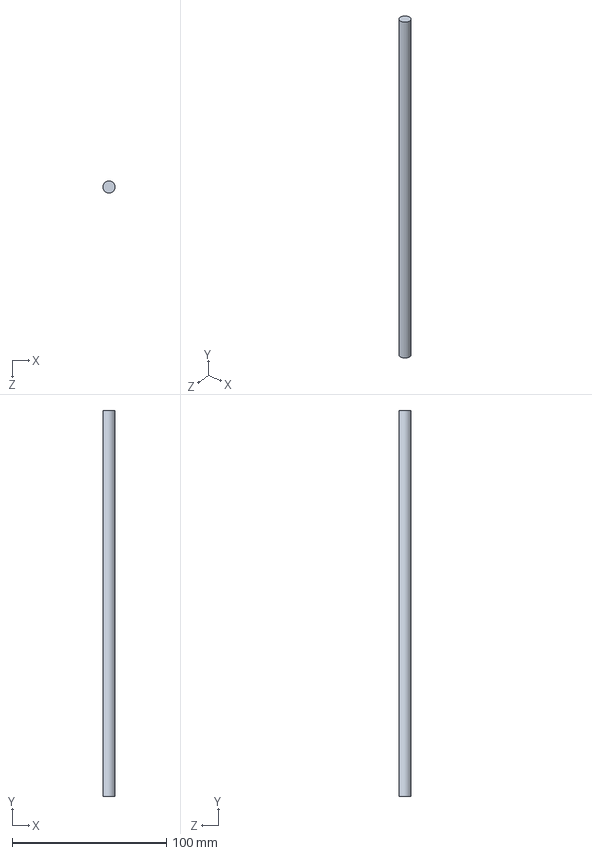
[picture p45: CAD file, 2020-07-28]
Mechanical Design/Trivision Bill Board/8mm shaft 25cm.SLDPRT
8.00 x 250.0 x 8.00 mm

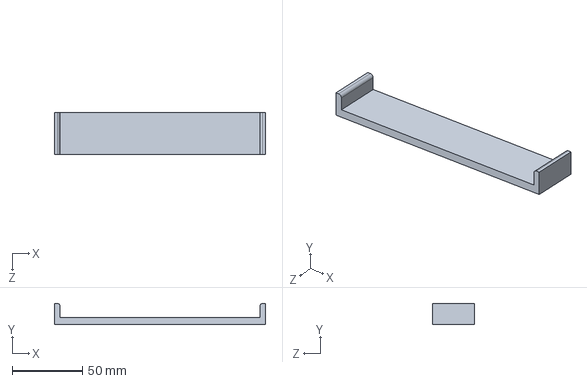
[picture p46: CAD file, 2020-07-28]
Mechanical Design/Biped Bot/Top _ Base.SLDPRT
150.0 x 15.0 x 30.0 mm

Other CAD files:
Mechanical Design/Trivision Bill Board/shaft 500mmL 8mmD.SLDPRT
Mechanical Design/Biped Bot/Central Shaft.SLDPRT
Mechanical Design/Trivision Bill Board/Triangular Prism.SLDPRT
Mechanical Design/Biped Bot/Coupling.SLDPRT
Mechanical Design/Biped Bot/Gear (0.5,1).SLDPRT
Mechanical Design/Biped Bot/Motor.SLDPRT
Mechanical Design/Biped Bot/Side Body.SLDPRT
Mechanical Design/Group Recruitment/Group_Recruitment_Cad.blend
Mechanical Design/Trivision Bill Board/shaft 8mm 4cm.SLDPRT
Mechanical Design/Trivision Bill Board/triangle 18cm.SLDPRT

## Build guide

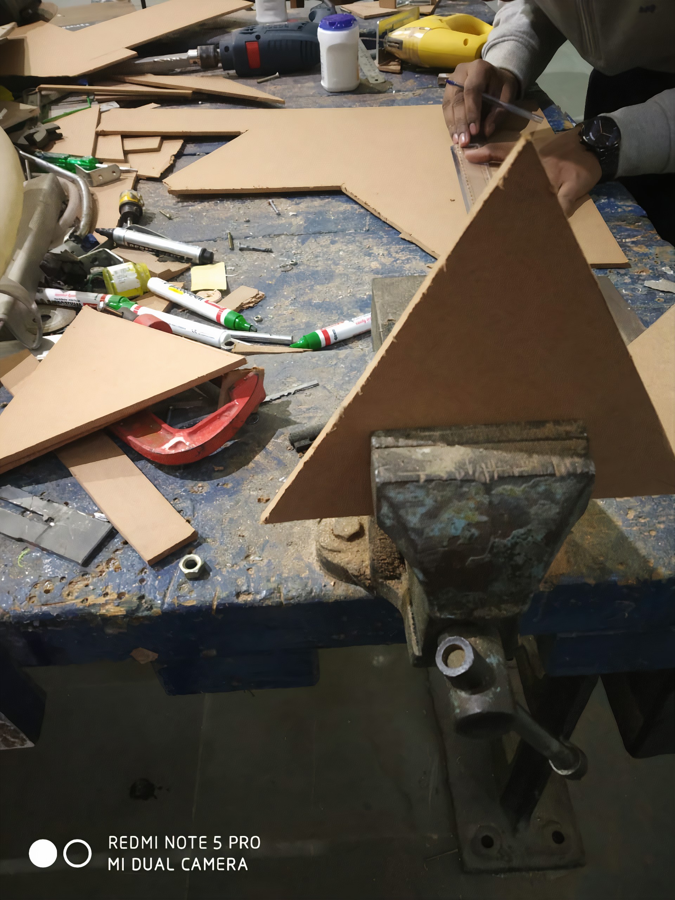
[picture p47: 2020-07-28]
Images and Videos/Images/Trivision_Base_Build.jpg

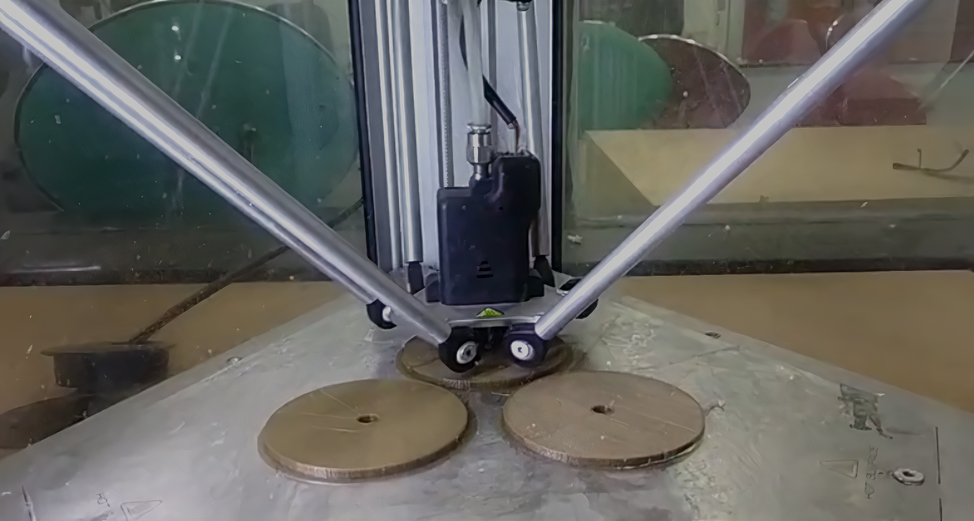
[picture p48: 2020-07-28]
Images and Videos/Images/Base_3D_Print.png

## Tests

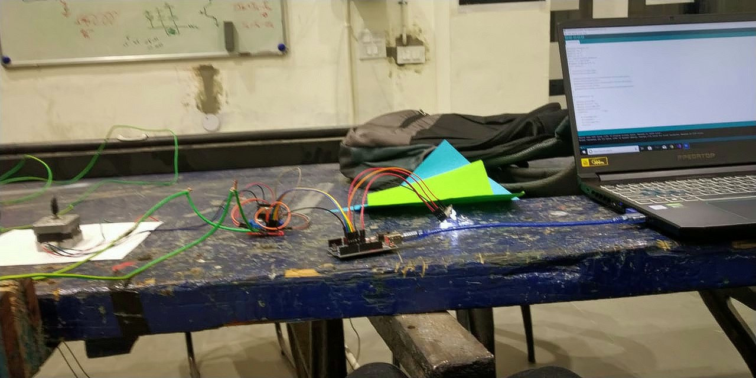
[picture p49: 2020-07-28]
Images and Videos/Images/Stepper_Motot_Test.jpeg

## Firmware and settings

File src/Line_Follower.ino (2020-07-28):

#include<SoftwareSerial.h>
int kp=15;                      
int kd=10;
int baseSpeed=50;
int maxSpeed=75;
int serialEn=2;
int pwm1=6;                     
int dir1=12;                  // Motor 1 direction
int pwm2=5;
int dir2=3;                   // Motor 2 direction
int base=35;
int pos;                      // Position detected by the LSA

SoftwareSerial SoftSerial(8, 7);

void setup() {
  pinMode(pwm1, OUTPUT);
  digitalWrite(serialEn,HIGH);
  digitalWrite(dir1,HIGH);
  digitalWrite(dir2,HIGH);
  pinMode(pwm2, OUTPUT);
  pinMode(dir1, OUTPUT);
  pinMode(dir2, OUTPUT); 
  pinMode(serialEn,OUTPUT);  
  SoftSerial.begin(38400);
  Serial.begin(38400); 
}

int lastError = 0;    

void loop() {
  digitalWrite(serialEn,LOW);
  Serial.println("abcd");
  while(!SoftSerial.available()){
    //Serial.println("abcd");
  }
while(SoftSerial.available()){
  pos=SoftSerial.read();
  Serial.println(pos);
}

if(pos == 255) {
  analogWrite(pwm1,0);
  analogWrite(pwm2,0);
}
else {
    int error = pos - base;   
    int motorSpeed = kp * error + kd * (error - lastError);   
    lastError = error;    
    int rightMotorSpeed = baseSpeed - motorSpeed;
    int leftMotorSpeed = baseSpeed + motorSpeed;
    if(rightMotorSpeed > maxSpeed) rightMotorSpeed = maxSpeed; 
    if(leftMotorSpeed > maxSpeed) leftMotorSpeed = maxSpeed;
    if(rightMotorSpeed < 0) rightMotorSpeed = 0;
    if(leftMotorSpeed < 0) leftMotorSpeed = 0;
    analogWrite(pwm2,rightMotorSpeed);
    analogWrite(pwm1,leftMotorSpeed);
    Serial.println(pos);
  }
}

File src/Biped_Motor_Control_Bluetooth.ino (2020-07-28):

#include <SoftwareSerial.h>
SoftwareSerial BlueTooth(5, 6);    // (TXD, RXD) of HC-06
char BT_input;                    // To store input character received via BT.
int motorPin1 = 8;                // Pin 2 on L293D IC
int motorPin2 = 9;                // Pin 7 on L293D IC

void setup() {
  BlueTooth.begin(9600);  
  Serial.begin(9600);
  pinMode(motorPin1, OUTPUT);
  pinMode(motorPin2, OUTPUT);
}

void loop() {
  if (BlueTooth.available()) {
   BT_input=BlueTooth.read();
    if (BT_input=='s') {
      digitalWrite(motorPin1, LOW);   
      digitalWrite(motorPin2, LOW);    
      Serial.println("Motor is Off");
    }
    else if (BT_input=='b') {
      digitalWrite(motorPin1, LOW);   
      digitalWrite(motorPin2, HIGH);  
      Serial.println("Motor is rotating left");
    }
    else if (BT_input=='f') {
      digitalWrite(motorPin1, HIGH); 
      digitalWrite(motorPin2, LOW); 
      Serial.println("Motor is rotating right");
    }
   else if (BT_input=='r') {
      digitalWrite(motorPin1, HIGH); 
      digitalWrite(motorPin2, LOW); 
      Serial.println("Motor is rotating right");
    }
    else if (BT_input=='l') {
      digitalWrite(motorPin1, LOW); 
      digitalWrite(motorPin2, HIGH);     
      Serial.println("Motor is rotating Left");
    }
  }
}

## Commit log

2020-07-27 Added cad files
    [Assembly.SLDASM, Assembly1.SLDASM, Central Shaft.SLDPRT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]
2020-07-28 Added poster and pathway cad
    [8mm shaft 25cm.SLDPRT, Assem1.SLDASM, Group_Recruitment_Cad.blend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]
